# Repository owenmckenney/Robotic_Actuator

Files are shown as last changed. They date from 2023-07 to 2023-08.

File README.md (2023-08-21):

# 3D printed Robotic Actuator

This robotic actuator provides high torque and speeds at a reasonable cost. It utilzes a moteus r4.11 bldc driver and a mj5208 brushless motor and has an 8:1 reduction. The components used are included in the [BOM](BOM.md). This actuator can be controlled through multiple different methods outlined in the [moteus documentation](https://github.com/mjbots/moteus), however the python files in this repo assume usage of a raspberry pi with a mjbots pi3hat r4.5. 

[Cad Overview](https://www.youtube.com/watch?v=ny0xnwEDxxo&ab_channel=OwenMcKenney)

## Specs

- Diameter: 82mm
- Width: 64mm
- ~2.5 Nm of torque

## Manufacturing & Assembly Tips

- Most components fit together intuitively as there is only one way that this actuator can be assembled. Only STL files are provided. For access to specifc source files, email owen.mckenney1@gmail.com. 
- The 3D printed components of the original implementation were printed on a Ender 3 using PLA. All components have a naturally built-in tolerance of 0.2mm; this value may not be perfect depending on the tuning of your printer. 
- The moteus r4.11 driver has 4 M2.5 mounting holes. For simplicity, this actuator uses only M3 components; in order to interface with M3 threaded inserts, these holes must be drilled out to 3mm. Drilling these holes has no percieved impact on the board.

## Setup

Before usage, the moteus r4.11 and mj5208 must be configured and calibrated per the steps outlined in the moteus documentation. Calibration must be carried out with nothing attatched to the motor.

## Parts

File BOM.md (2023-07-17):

# Bill of Materials

- moteus r4.11 - [link](https://mjbots.com/products/moteus-r4-11)
- mj5208 brushless motor - [link](https://mjbots.com/products/mj5208)
- 50x65x7mm bearing - [link](https://www.amazon.com/dp/B082PXZLJT?psc=1&ref=ppx_yo2ov_dt_b_product_details)
- 4x9x4mm bearing - [link](https://www.amazon.com/dp/B07FW1958S?psc=1&ref=ppx_yo2ov_dt_b_product_details)
- 4x20mm stainless steel dowel pins (4x) - [link](https://www.amazon.com/dp/B07MNVTFW4?psc=1&ref=ppx_yo2ov_dt_b_product_details)
- M3 threaded inserts - [link](https://www.amazon.com/dp/B087NBYF65?psc=1&ref=ppx_yo2ov_dt_b_product_details)
- 8mm M3 socket head cap screws (at least 8x, up to 16x)
- 12mm M3 socket head cap screws (7x)

All listed components can be purchased for roughly $200. All links are merely recommendations, parts can likely be sourced from other sellers (apart from moteus and mj5208).

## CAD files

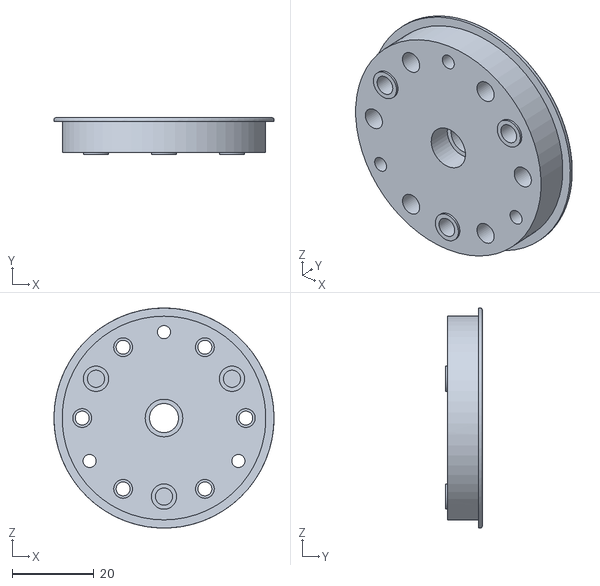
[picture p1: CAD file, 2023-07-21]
hardware/Carriage.STL
53.8 x 9.00 x 53.8

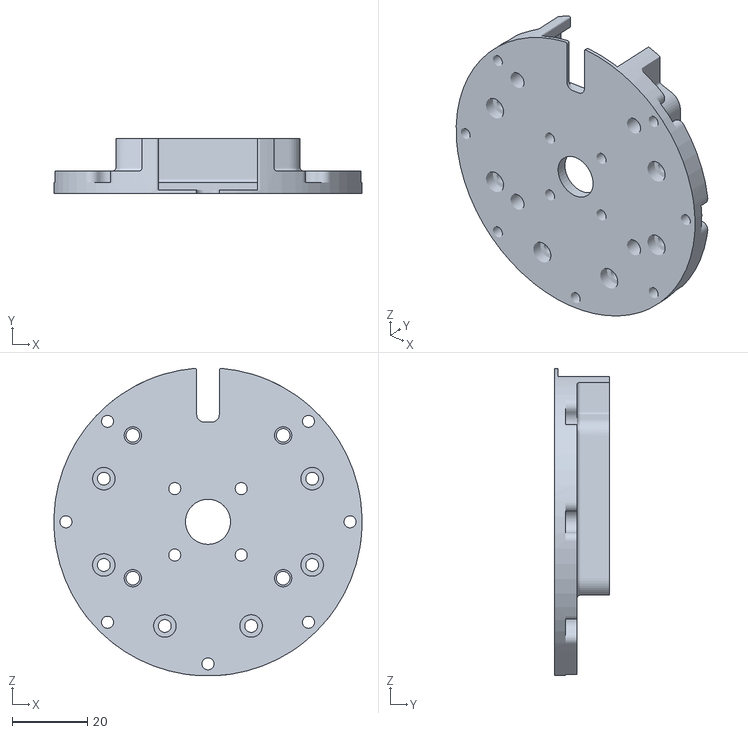
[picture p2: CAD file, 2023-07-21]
hardware/Ring Base.STL
82.0 x 14.7 x 81.8

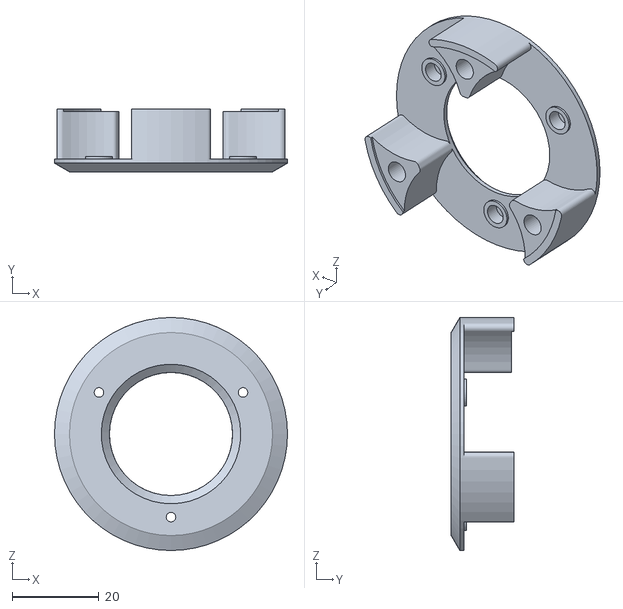
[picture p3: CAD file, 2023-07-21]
hardware/Planet Stabilizer.STL
53.8 x 14.5 x 53.8

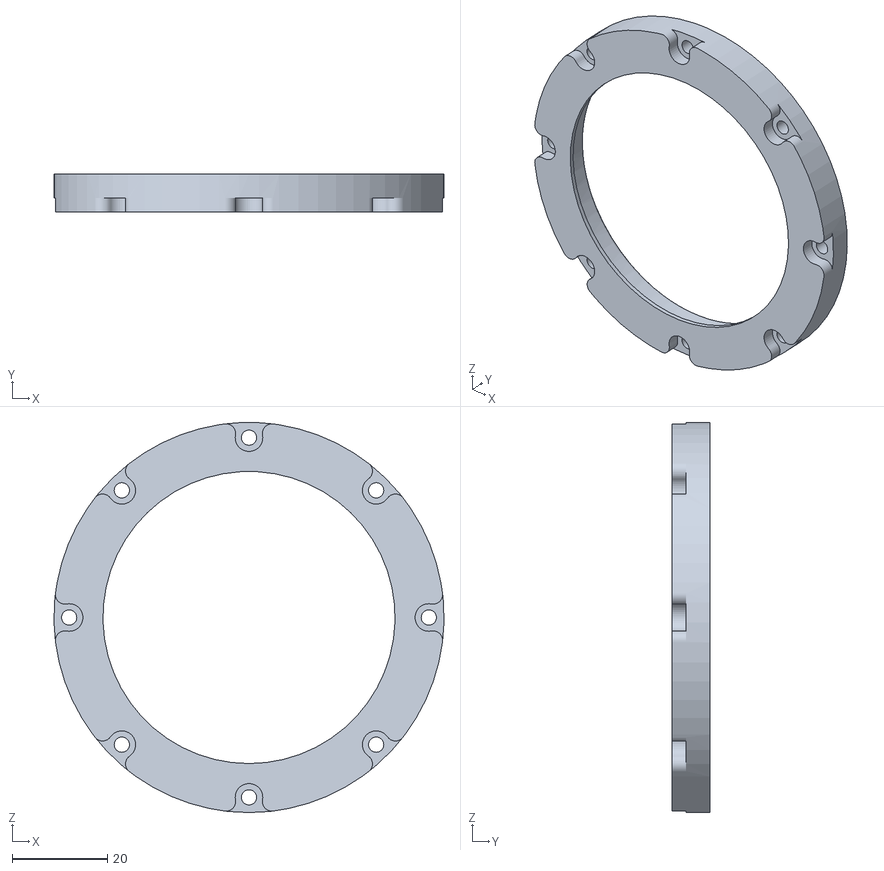
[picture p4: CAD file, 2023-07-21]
hardware/Ring Lid.STL
82.0 x 8.00 x 82.0

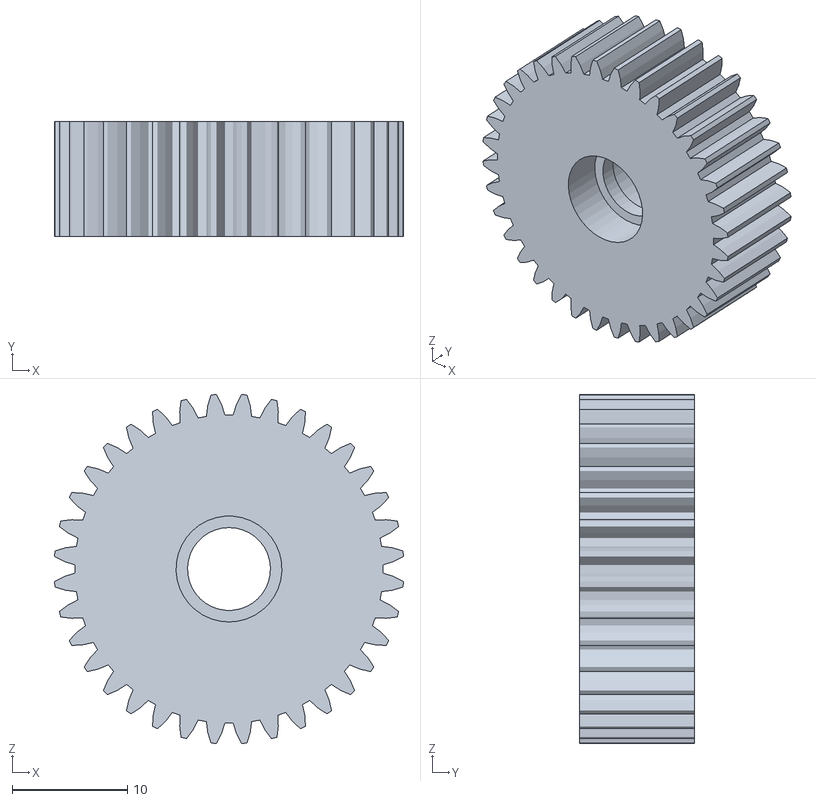
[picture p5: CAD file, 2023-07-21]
hardware/Planet.STL
30.3 x 10.0 x 30.3

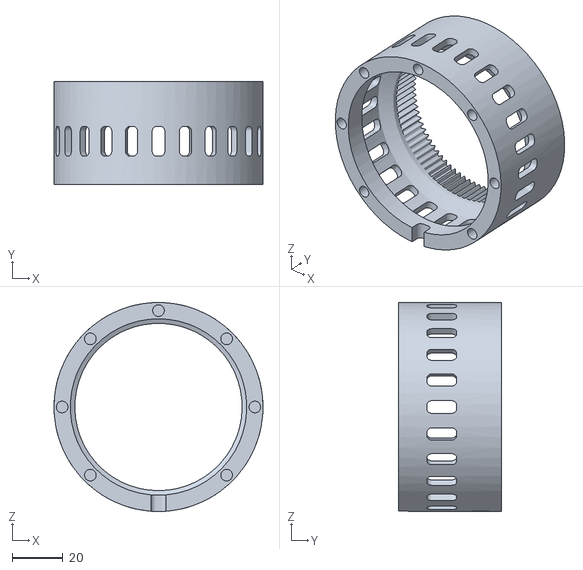
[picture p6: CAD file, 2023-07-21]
hardware/Ring.STL
82.0 x 40.3 x 82.0

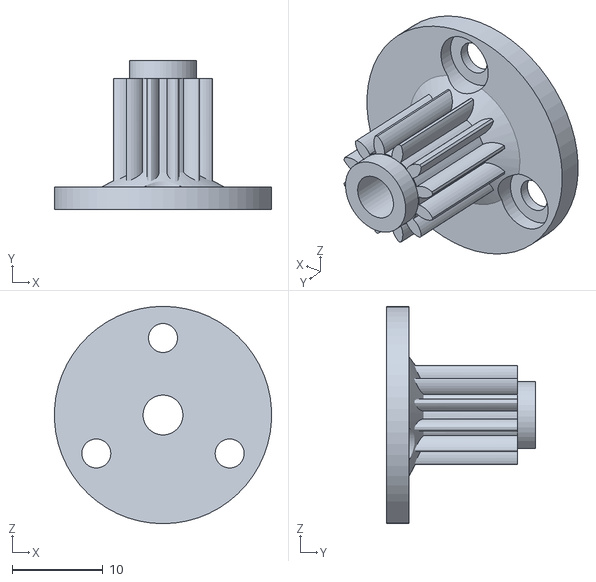
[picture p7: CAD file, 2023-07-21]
hardware/Sun Gear.STL
24.0 x 16.5 x 24.0

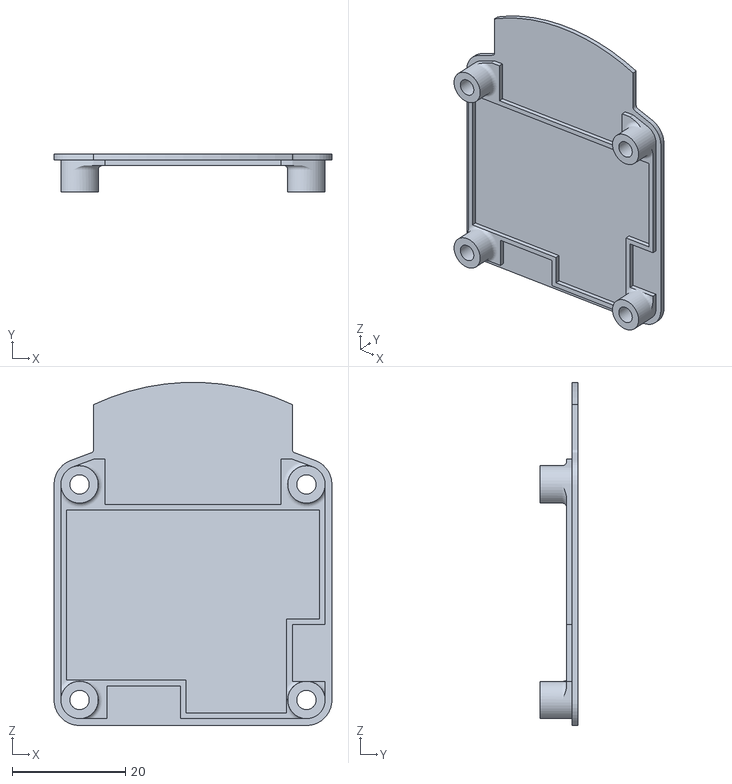
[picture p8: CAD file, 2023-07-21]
hardware/Board Lid.STL
49.0 x 6.65 x 60.5

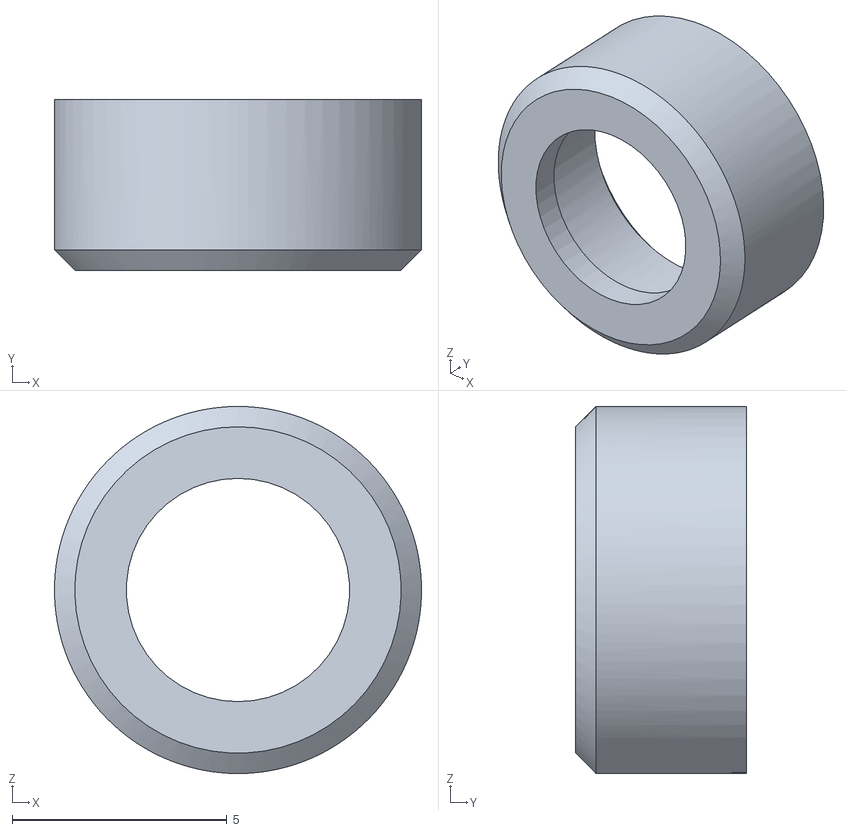
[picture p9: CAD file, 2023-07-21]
hardware/Magnet Holder.STL
8.55 x 3.98 x 8.55

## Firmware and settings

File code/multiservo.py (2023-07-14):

# rotates two servo motors on CAN bus 1 ID 1 and ID 2
# rotation time is not synced (spinning ID 1 clockwise 2 rotations
# and ID 2 clockwise 1 rotation will not complete simultaneously however 
# they will start simultaneously)

import math
import time
import asyncio
import moteus
import moteus_pi3hat

async def main():
    transport = moteus_pi3hat.Pi3HatRouter(
        servo_bus_map = {
            1:[11],
            2:[11]
        }
    )

    s1 = moteus.Controller(id=1, transport=transport)
    s2 = moteus.Controller(id=2, transport=transport)

    await s1.set_stop()
    await s2.set_stop()

    while True:
        s1_command = round(float(input("Enter desired pos for servo 1")), 2)
        s2_command = round(float(input("Enter desired pos for servo 2")), 2)

        commands = [
            s1.make_position(
                position = s1_command,
                velocity = 0.0,
                accel_limit = 2.0,
                velocity_limit = 1,
                maximum_torque = 0.15,
                watchdog_timeout = math.nan,
                query = True
                ),
            s2.make_position(
                position = s2_command,
                velocity = 0.0,
                accel_limit = 2.0,
                velocity_limit = 1,
                maximum_torque = 0.15,
                watchdog_timeout = math.nan,
                query = True
                )
            ]

        states = await transport.cycle(commands)

if __name__ == '__main__':
    asyncio.run(main())

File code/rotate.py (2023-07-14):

# rotates a single servo motor on CAN bus 1 ID 1

import asyncio
import moteus
import time
import math
import sys

async def main():
    c1 = moteus.Controller()
    await c1.set_stop()

    while True:
        pos = input("entire desired postion: ")

        if pos == 'exit':
            sys.exit("")
        
        pos = round(float(pos), 2)
 
        state = await c1.set_position(
                position=pos, 
                velocity=0.0,
                accel_limit=2.0,
                velocity_limit=5,
                maximum_torque=0.075,
                watchdog_timeout=math.nan,
                query=True
                )
        
        print(state)
        print()

        await asyncio.sleep(0.02)

asyncio.run(main())
